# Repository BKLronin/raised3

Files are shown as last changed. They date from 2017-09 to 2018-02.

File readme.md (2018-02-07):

# raise-d³ #

## Description ##

FDM printer for remote operation with octoprint for flexible small scale production. Designed from scratch and inspired by the I3 by Josef Prusa, MP3DP by Ryan Zellar and the Itopie by Skarab

### Key features ###

Print volume: 250 x 270 x 250

Made from 12mm beechplywood "Multiplex"

Exchangeable extrudermount with E3D Titan Aero as suggested standard. Should fit a MK8 Style extruder and hotend as well. 

The electronic parts are all kept within the main case and get cooled by two 60mm fans.

Not designed yet but should work with a small spindle like Proxxon or Dremel for carving PCB production.

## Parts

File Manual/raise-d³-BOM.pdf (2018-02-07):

Raise-d³ | BOM
| Mechanik
Bauteil | Anzahl | Beschreibung | Preis in EUR | Quellenbeispiel
D³ – Multiplex Rahmenset | 1 | Buchenmultiplexrahmen cnc gefräst | 119 | Raise-Shop, selbst
Gedruckte Teile Set | 1 | PLA/PETG | 89,99 | Raise-Shop, selbst
Aluminumbett | 1 | 6mm feinstgefräst | 25 | B&T Metall
Präzisionswelle 400mm | 4 | Gehärtet h6¹ | 25 | Dold_Mechatroni k
Präzisionswelle 390mm | 2 | Gehärtet h6 | 15 | Dold
Wellenhalter H10 stehend | 8 | Kann gedruckt werden | 30 | Dold
LM10UU Lager | 12 | Gedruckte oder IGUS lager möglich | 5 | Dold
Kugellager 608 | 3 | Für Y Riemen umlenk, Spule | 1 | Dold
Kugellager ID4mm | 1 | Für X idler
GT2 Riemen X | 1 | 1m
GT2 Pulley | 1 | 21 Zähne | 2
HTD Riemen Y | 1 | 1m HTD3m 9mm, PU | | Dold
HTD Pulley | 1 | 20 Zähne HTD3m, 9mm, breit 5mm Bohrung | | Dold
Gewindespindel | 2 | TR 8x1,5, 300mm, Alternativ integrierte von anycubic | 5 | Dold
Kupplung | 2 | 5mm auf 8mm. Gedruckt TPU | 5 | raise-shop
M4 x 16 | 70
M4 x 20 | 11
M4 x16 senk | 16
M4 x25 | 2
M3 x20 | 4
M3 x30 | 1
M3 x16 | 22
M3 x40 /2x 16 | 1/2
M3 x10 | 12
M3 Mutter Selbstsichernd | 18
| | | 0

Elektronik
Bauteil | Anzahl | Beschreibung | Preis in EUR | Quellenbeispiel
Steppermotor | 4 | 4 x Nema 17 | 50 | stepper-online
Mainboard | 1 | Megatronics / Minitronics | 90/50 | reprapworld
Rapsberry Pi3 | 1 | + Sd Card | 40 | reichelt
Raspicam | 1 | Optional + längeres Flachband | 25 | teichelt
Netzteil | 1 | Meanwell 10A(LRS-100-12 ) für Silikon oder 30 A für das kleinere MK2ish Heizbett | | Rs components
Heizmatte | 1 | 250 x 250 mm 230V | 50 | filafarm
SSR | 1 | 12V DC in 230 V Schalt | 20 | reichelt
Hotend/Extruder | 1 | E3D Titan Aero | 130 | E3D-online
Hauptschalter | 1 | WS R13-112 LPLB | 1 | reichelt
Sicherung | 1 | TR 3,15 A | ,2 | reichelt
Kaltgerätestecker | 1 | KES 2SI | | reichelt
Lüfter Radial | 1 | EBM Papst RLF35 | 25 | rs-components
Lüfter Hotend | 1 | EBM Papst 412 (optional) | 15 | reichelt
Lüfter Gehäuse | 2 | Skythe MK60 | 9 | reichelt
5V 2A Regulator | 1 | Servo + Raspi (RECOM) | 5 | reichelt
Servo 9g | 1 | Hitec HS65 / KDS | 20
Sum | 390,2

1

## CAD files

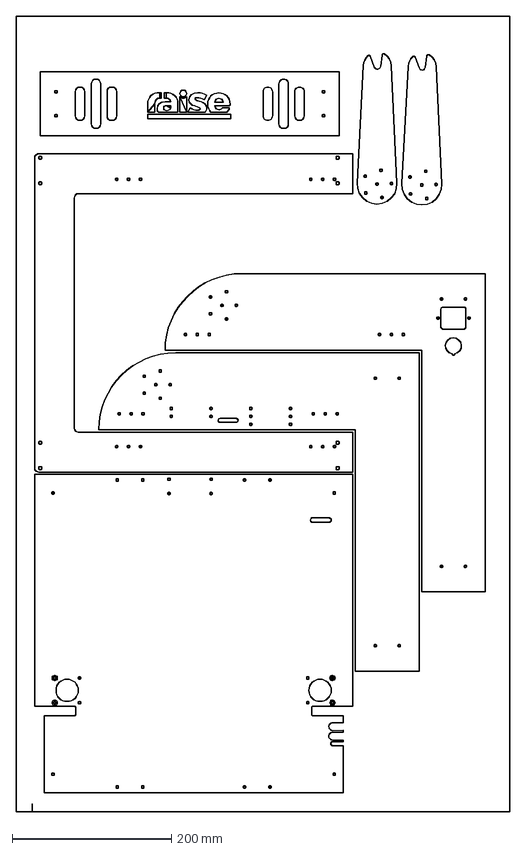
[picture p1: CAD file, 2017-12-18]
Milled_Parts/#raiseuav komplett 2017_09_16.dxf
620.0 x 1000.0 mm

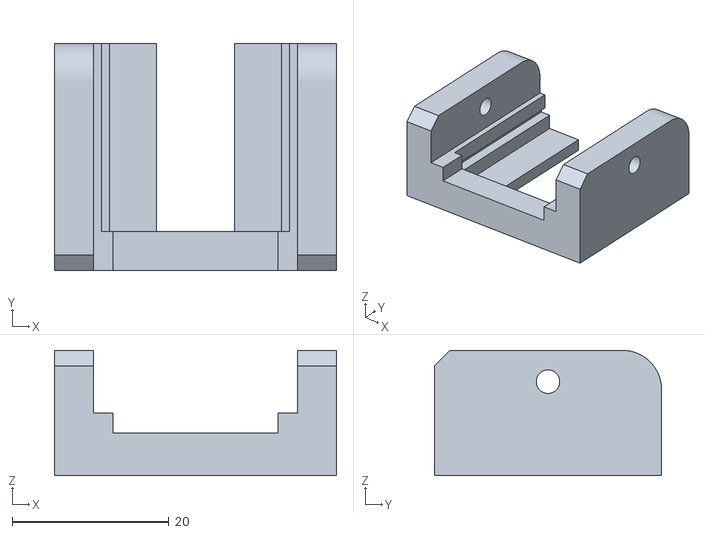
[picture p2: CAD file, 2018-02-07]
Printed_Parts/raspicam_arm_pcb.stl
36.0 x 29.0 x 16.0

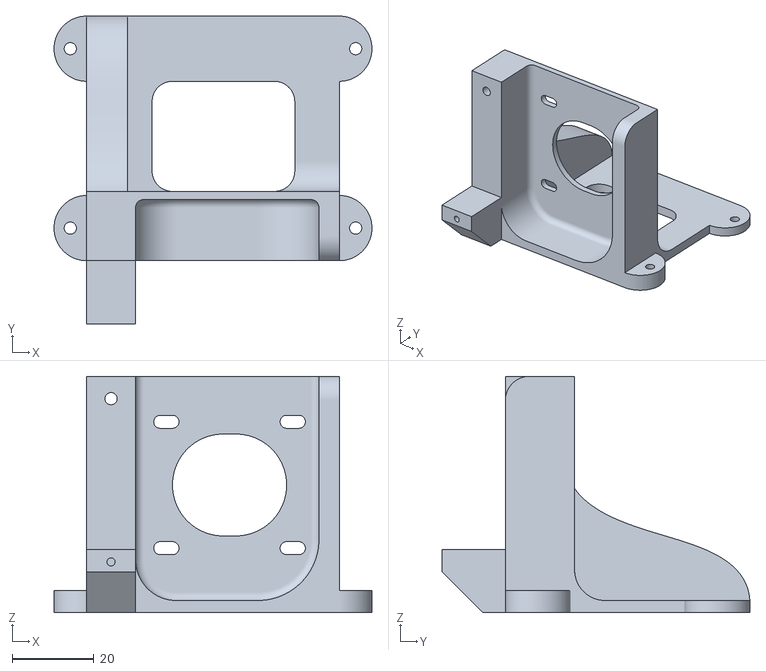
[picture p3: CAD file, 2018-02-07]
Printed_Parts/Aero_Frame.stl
78.0 x 75.5 x 58.0

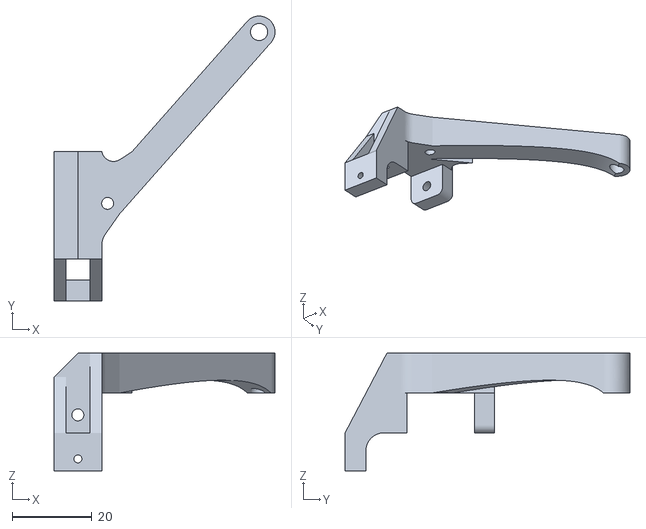
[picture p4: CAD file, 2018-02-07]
Printed_Parts/Axialfan_Mount.stl
55.5 x 71.5 x 29.5

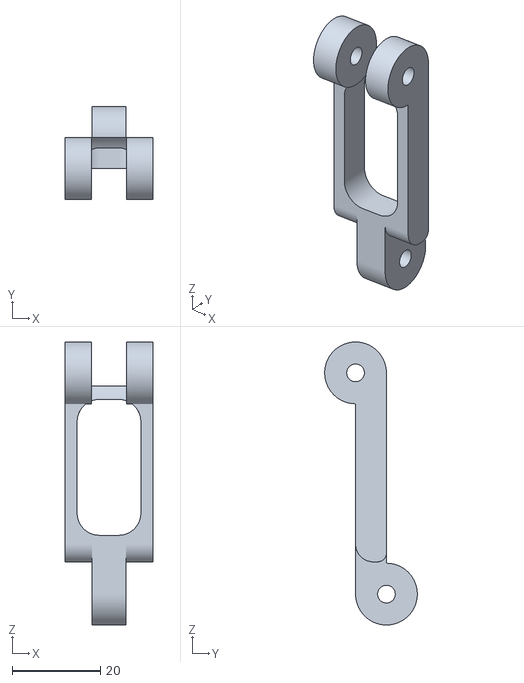
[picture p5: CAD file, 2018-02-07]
Printed_Parts/raspicam_arm_lower.stl
20.0 x 20.9 x 64.0

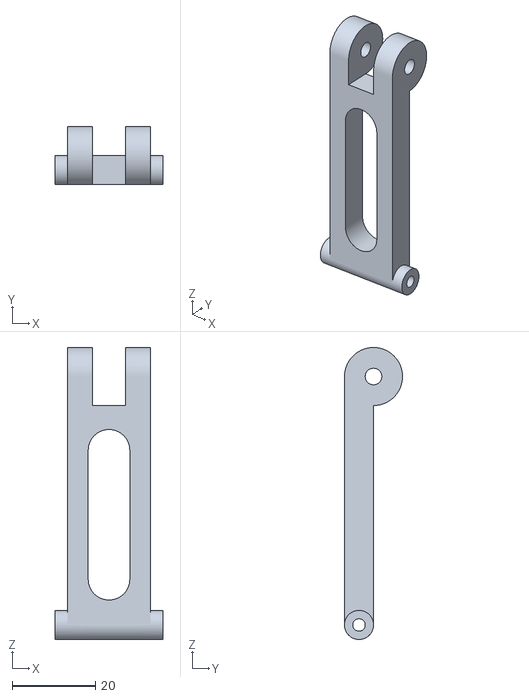
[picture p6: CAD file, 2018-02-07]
Printed_Parts/raspicam_arm_upper.stl
26.0 x 14.0 x 70.2

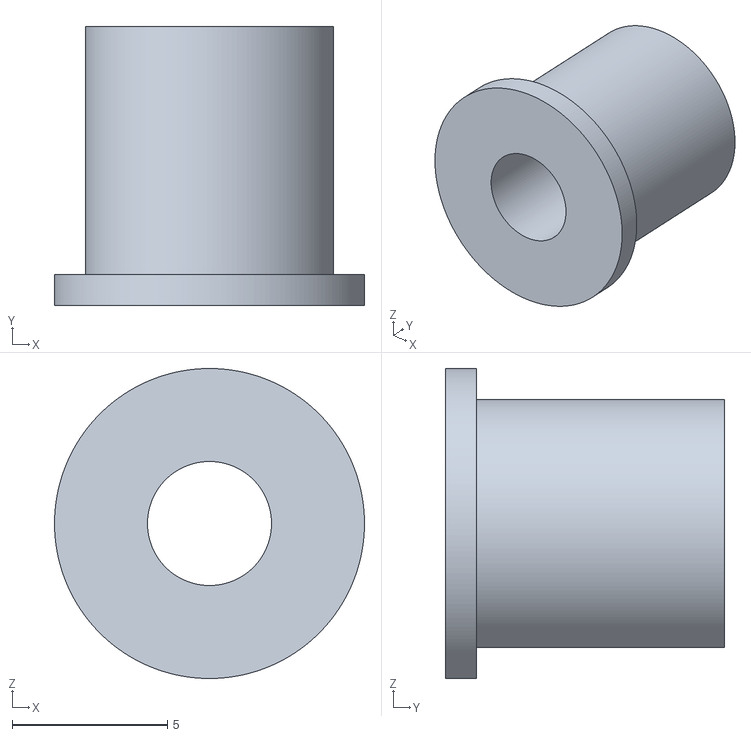
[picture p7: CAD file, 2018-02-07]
Printed_Parts/Y-608Adapter8-4.stl
10.0 x 9.00 x 10.0

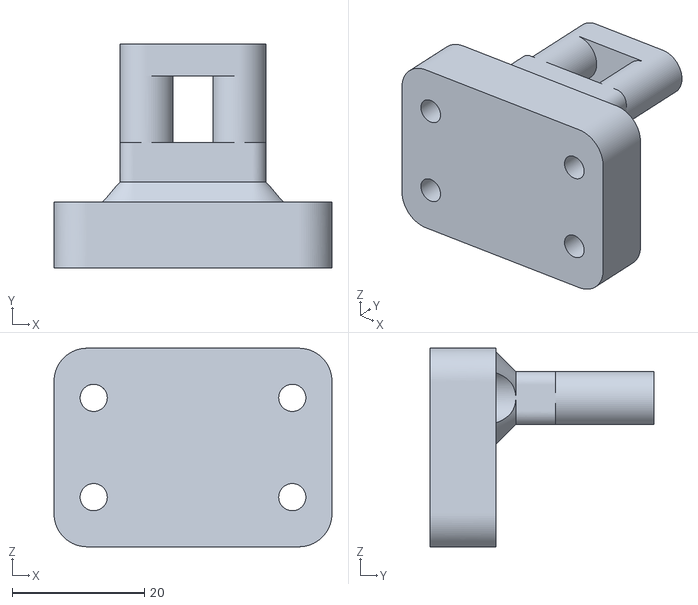
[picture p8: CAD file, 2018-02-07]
Printed_Parts/Y-Bed-Belt_Anchor_NewB.stl
42.0 x 33.9 x 30.0

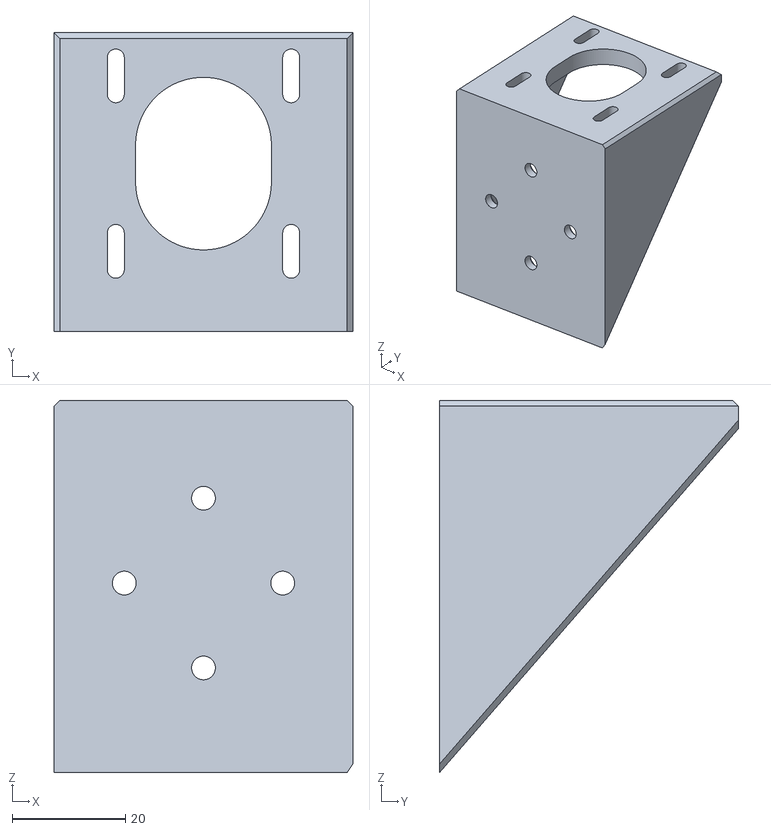
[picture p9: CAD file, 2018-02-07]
Printed_Parts/Nema17-Y-Stepper_Holder_AdjustB.stl
52.8 x 52.8 x 65.8

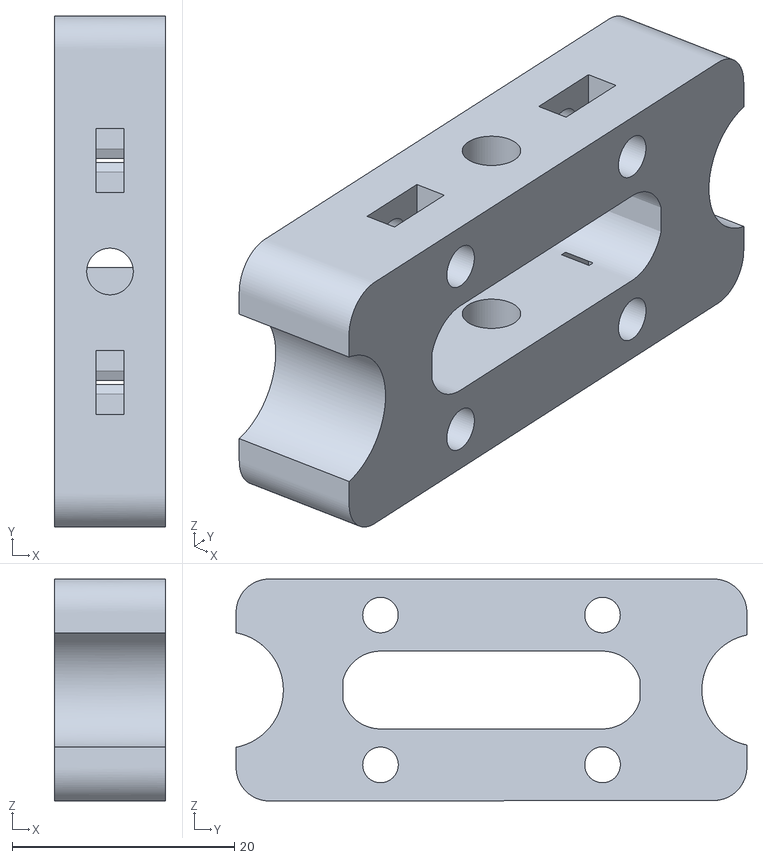
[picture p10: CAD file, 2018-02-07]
Printed_Parts/X-Bearing_Holder_AdjustB(Alternat).stl
10.0 x 46.0 x 20.0

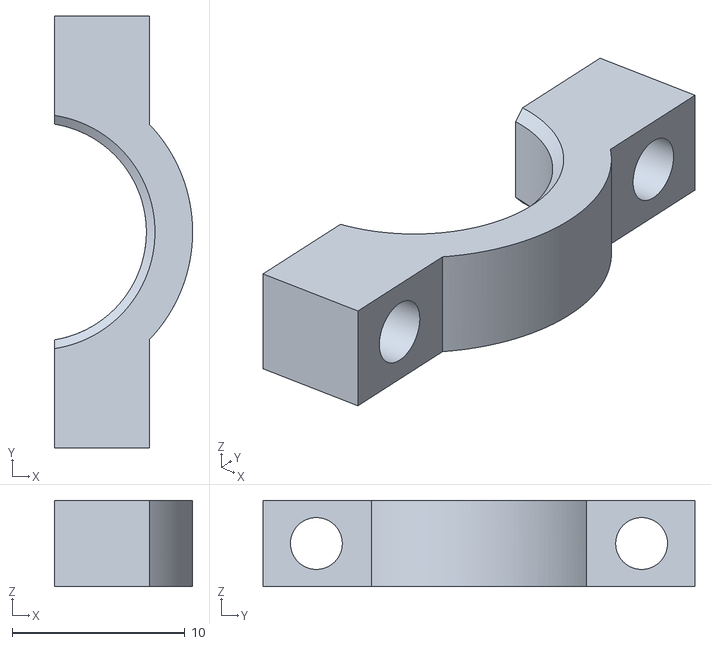
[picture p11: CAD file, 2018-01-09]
Printed_Parts/X-carriage_cable.stl
8.00 x 25.0 x 5.00

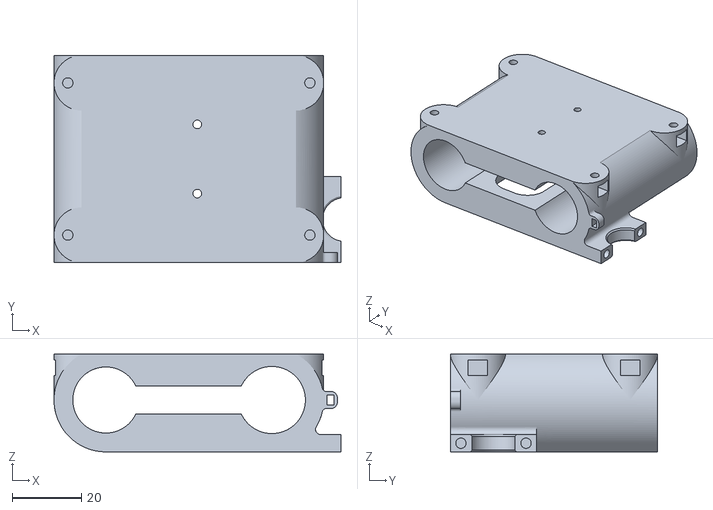
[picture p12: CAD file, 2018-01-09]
Printed_Parts/X-carriage.stl
83.0 x 60.0 x 28.3

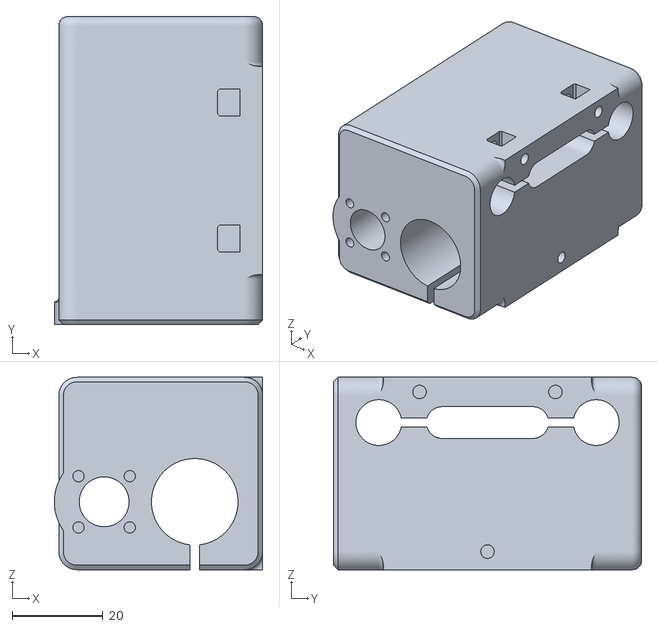
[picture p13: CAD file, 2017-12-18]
Printed_Parts/XZ-Block_right.stl
46.0 x 68.0 x 42.5

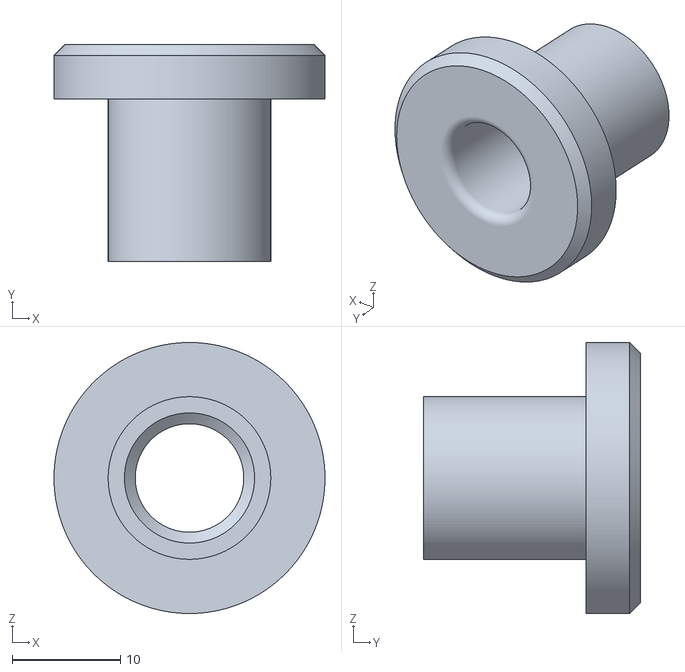
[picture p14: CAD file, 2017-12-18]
Printed_Parts/Cableduct_bed.stl
25.0 x 20.0 x 25.0

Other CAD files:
Printed_Parts/Nema17-Y-Stepper_Holder.stl
Printed_Parts/XZ-Block_left.stl
Printed_Parts/raspicam_arm_foot.stl
Printed_Parts/Y-Beltbed_adjustment_Stat.stl
Printed_Parts/Angle_Portal.stl
Printed_Parts/BedEdgeclamp.stl
Printed_Parts/Cooling_Exhaust.stl
Printed_Parts/Fanduct.stl
Printed_Parts/FrameAngle_lower.stl
Printed_Parts/Nema14_Stepper_Holder.stl
Printed_Parts/SpoolDrum.stl
Printed_Parts/SpooldrumNut.stl
Printed_Parts/TPU_coupling30pctI.stl
Printed_Parts/X-Bearing_Holder.stl
Printed_Parts/X-BeltClamp.stl
Printed_Parts/Y-Bearing_Holder.stl
Printed_Parts/Y-Bed_Bearing_holder.stl
Printed_Parts/Y-Beltbed_adjustment_Move.stl

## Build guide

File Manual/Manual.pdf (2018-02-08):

raise-d³ | Handbuch

## Inhaltsverzeichnis

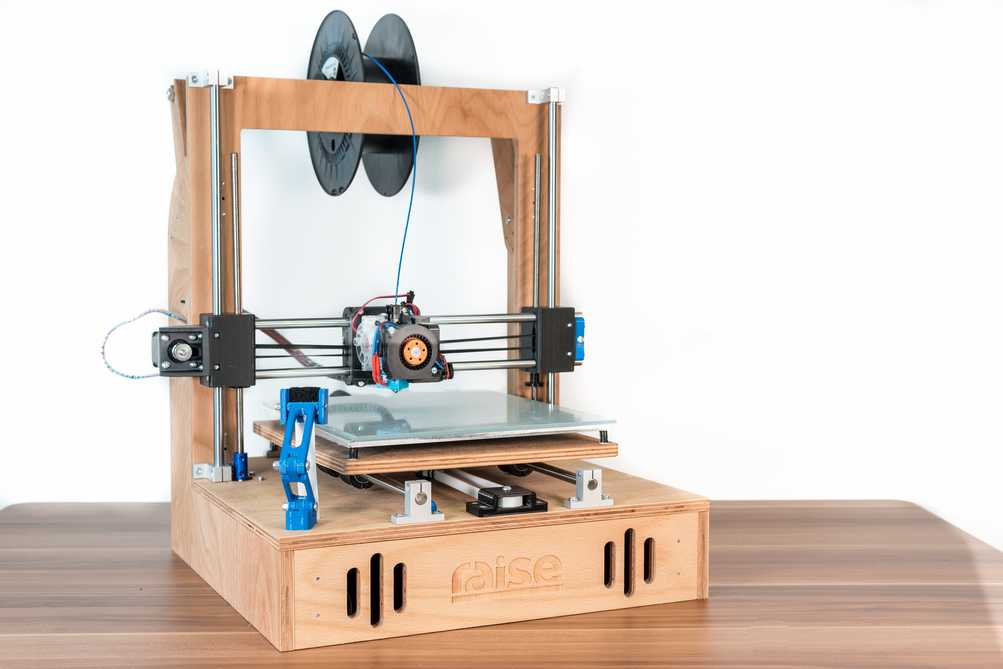
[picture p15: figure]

## 1. Introduction

## 1.1. Safety instructions

The printer has a number of safety circuits, but never leave it unattended.

Do not lift the printer while the power plug is plugged in. There is a risk of electric shock.

Keep the pressure chamber clear. Handling within the installation space can cause injuries.

Never touch the heating components while the printer is switched on, as this may cause burns.

Use suitable fire extinguishers in case of fire to avoid the danger of an electric shock.

Have maintenance work on the electronics and mechanics carried out by a service technician to prevent damage.

The current-carrying components should be connected by a trained electrician (VDE)! The company raise-UAV assumes no liability for damages and injuries resulting from faulty installations.

## 2. Build the Printer

## 2.1. Manufacturing of the frame

Beech plywood with a thickness of <= 12mm was used for the frame. The panels have a maximum dimension of 400mm in all directions. A little reserve when milling is to be considered. Milling was done with a 3mm universal 2-flute or 3mm diamond cut.

Milling parameters for beech plywood (MPCNC):
400 mm/min at 3mm immersion depth conventional (clockwise)
800W spindle at 30000 revolutions

Panel blanks with 450 x 450mm were used, which enables individual turning of the panels so that during assembly the curvature lies outside and can be pulled against the milling edge.
When drilling the holes (CNC), a helical movement of at least 0.5mm (at 3mm milling cutter) must be observed to ensure chip removal.

The holes should not exceed 3.5mm as these threads are drilled with a 4mm tap.
All 3mm holes in the drawing are therefore provided with an M4 thread which is necessary for the connection with the printed angles.

### 2.2 Post processing the plates

Grinding was done with a triangular grinder (depending on availability) to get the surface as smooth as possible for impregnation.
Polyboy wood oil has proved its worth since it cannot ignite itself and offers sufficient protection of the wood without toxic components. It can also be used indoors without the risk of solvents in the room air. Alternatively, the panels can of course also be painted. The oil is ideally applied after the frame has been mounted to relieve a bit of the tension.

## 2.3 Printing the parts

All parts can be printed in PLA with a minimum infill of 30%. The Nema14/17X holder should be made of temperature-resistant materials. In this case Greentec was used which withstands temperatures up to 60°C without any problems. With the larger Nema17 mount, the temperature is expected to be lower, so PLA or better PETG is completely adequate at this point. The extrudermount for the Titan Aero or MK8 extruder can also be printed from more thermostable materials.

## 2.4. Frame assembly

The frame is held together by two types of angles. They compensate and dampen possible distortion in the plywood panels and are easy to produce.

The angles are fixed with M4 x 16 mm screws in the previously cut threads in the plywood panels M4. Explosionsanimation (https://www.youtube.com/edit?o=U&video_id=dvnm-ai_ZwE)

Start with the two side panels, the base plate, the front and back plates. It is recommended that the installation is carried out on a level ground. When tightening the screws make sure that nothing is distorted. The frame is largely self-aligning. Finally, the portal with any existing curvature is inserted in the direction of the logo and pulled backwards with the portal angles against the side panels.

•

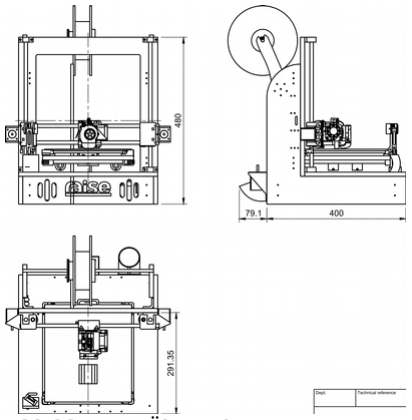
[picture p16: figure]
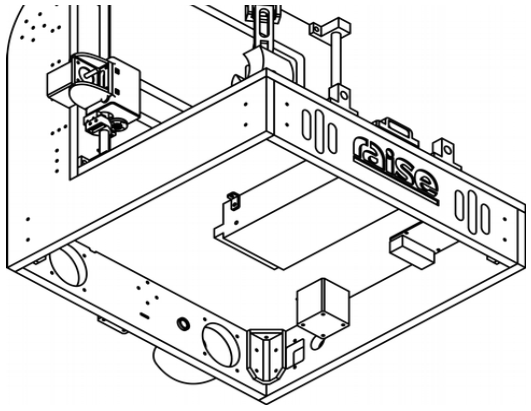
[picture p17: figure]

Abbildung 1: Übersicht | Abbildung 2: Position Winkel

## 2.5 Component placement

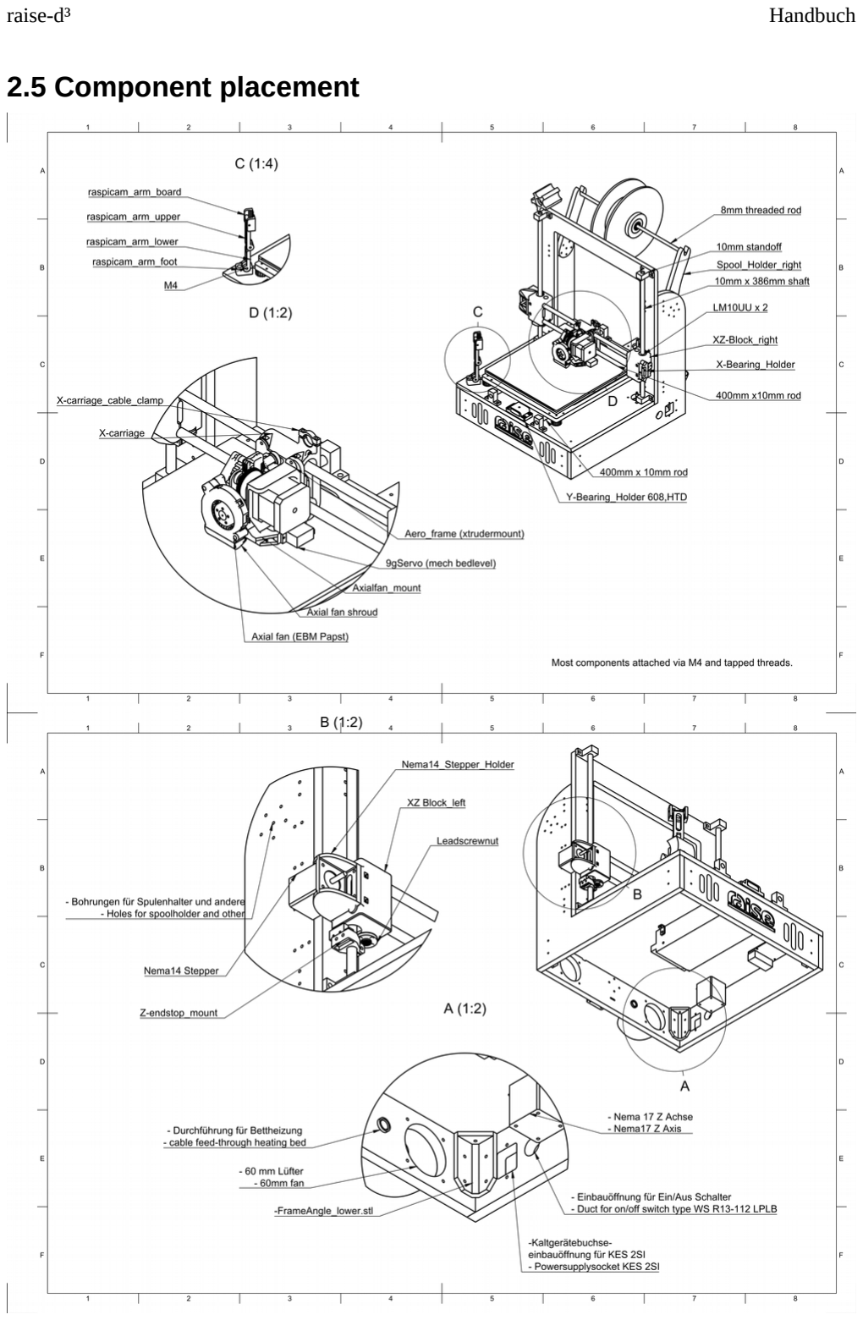
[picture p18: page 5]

## 2.6. Axis installation

### 2.6.1 Y-Axis

Push the LM10UU bearings into the "Y-Bed_Bearing_holder" and loosely screw them with M4x16 onto the underside of the bed. The bearings are fixed with M3 x 20 in the holders. Take one of the 10 x400mm precision shafts and slide it into the bearings to align them. While the shaft is in it, tighten the brackets crosswise. The shaft should move easily. Repeat this procedure for the second page.

Screw the belt holder "Y-Beltbed_adjustment_Stat" with four M4 x 16 screws to the underside of the bed. Insert an M3 locknut into the hexagon nut on the fixed side (Fig.
4) and an M3x30 into the movable side (Fig. 5). The movable side is now inserted into the T_slot of the fixed side and tightened slightly with the M3 screw. These two parts later ensure that the Y-belt is tensioned.

Fasten the "Nema17-Y-Stepper_Holder" (Fig. 6) to the rear of the frame with four M4x16 screws and a Nema 17 with approx. 40N/cm with M3 x16 loose in it. Attach the HTD Pulley to the axis of the stepper.
Screw the "Y-Bearing_Holder" (Fig. 7) with countersunk head M4 x 16 onto the base plate and fix a 608 ball bearing with washers in it. There is an adapter for the M8 to M4 in the printed parts directory.

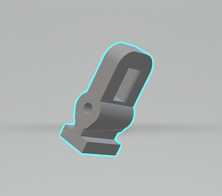
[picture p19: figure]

Guide the strap through all components around the pulley and secure it as tightly as possible on both sides of the tensioning mechanism with cable ties. It is recommended to fix one side of the Y-mechanism on the base plate with M4 x16 and to tilt the bed slightly when tightening. Continue tightening the belt by tightening the stepper motor and after securing the second linear guide, adjust the tension to the desired tension using the M3 screw on the belt attachment.

The aluminium bed is made of a finely milled cast aluminium piece of 250x280x6mm. The holes correspond to those in the bed and are screwed with M4 countersunk head screws and springs into the M4 threads of the bed.

An insight into the alignment of an older version of the printer is given below hier (https://youtu.be/frliOqVh3j4?t=1m12s)

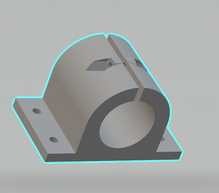
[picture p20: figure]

Abbildung 3

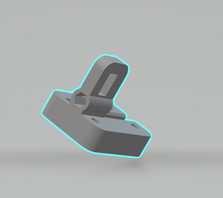
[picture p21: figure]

Abbildung 4

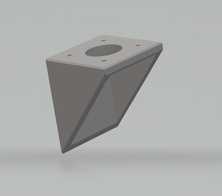
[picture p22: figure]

Abbildung 6

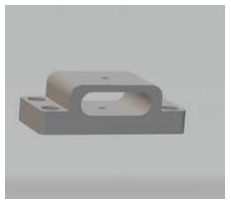
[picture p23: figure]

Abbildung 7

Abbildung 5

### 2.6.2 X-Axis

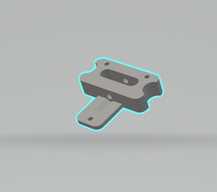
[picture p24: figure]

Drill the holes in part "XZ-Block_left" and "XZ-Block_right" as shown in Figure 9, attach the "Nema14_Stepper_Holder" to the left X-Z block with M3 x 16 and corresponding lock nuts.
Insert the 10 x 400 mm precision shaft into the 10 mm openings up to the stop of the stepper holder in the left X-Z_Block, where more force may be required.
Drill all holes to 3mm. Take four LM10UUU bearings and slide them into the "Xcarriage" (Fig. 11). Then push it onto the rods. If the bearings are too loose, they can be locked with a layer of tesa.
Slide the "XZ-Block_right" onto the two shafts and attach the "X-Bearing_Holder" to the "XZ-Block_right". The shafts should be flush with the surface of the bearing support + 2mm, for example, the exact alignment is done when merging with the Z-axis.
Drill the "X-BeltClamp" (Fig. 12) to 3mm and fasten it in the pocket of the "Xcarriage" with long enough M3 and nuts on the opposite side.
Connect the stepper motor and the moving part to the GT2 belt through the bearing on the opposite side. Leave the stepper loose so that you can retighten it later.

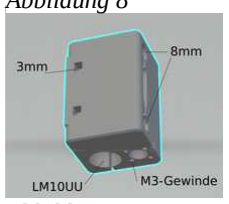
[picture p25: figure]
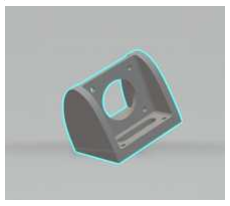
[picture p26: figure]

Abbildung 10

Abbildung 8

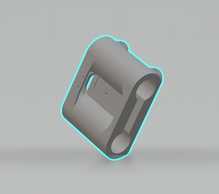
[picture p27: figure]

Abbildung 11

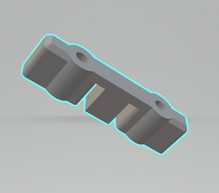
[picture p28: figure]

Abbildung 12

Abbildung 9

### 2.6.3 Z-Axis

Install the Nema17 Stepper with M3 screws in the base plate. Now screw the lower shaft holders into the holes of the portal. Then they take the 390mm precision shafts and insert them into the holders as far as they will go. Screw the guide spindles into the spindle axis nuts of the X-axis and guide the entire assembly on both sides onto the Z-axis shafts. Couple the leadscrews with the stepper motors in the base plate to the printed TPU coupler (or other). Alternatively: Integrated leadscrews. Now install the upper shaft holders.
Check the distance of the X-Z-blocks to each other and make sure that they do not cause any tension between the Z-shafts. Correct these if necessary.

Translated with www.DeepL.com/Translator

1. Einfuehrung
1.1. Sicherheitshinweise
1.2. Lieferumfang
1.3. Technische Details
2. Montage des Druckers
2.1. Aufbau des Rahmens
2.2. Installation der Linearmechanik
2.3. Installation der elektronischen Komponenten
2.4. Verkabelung
2.5. Ausrichten des Druckbetts
3. Software
3.1. Cura installation
3.2. WLAN Einrichtung
3.3. Koppeln des Druckers mit Cura
4. Allgemeiner Workflow
5. Support
6. Rechtliches

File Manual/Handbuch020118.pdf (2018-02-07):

raise-d³ | Handbuch

## Inhaltsverzeichnis


## 1. Einfuehrung

## 1.1. Sicherheitshinweise

Der Drucker verfügt über eine Reihe von Sicherheitsschaltungen, lassen sie ihn dennoch niemals unbeaufsichtigt.

Heben sie den Drucker nicht an solange der Netzstecker am Gerät eingesteckt ist. Es besteht die Gefahr eines elektrischen Schocks.

Halten sie den Druckraum frei. Das hantieren innerhalb des Bauraums kann zu Verletzungen führen.

Berühren sie niemals die Heizkomponenten während der Drucker eingeschaltet ist, dies kann zu Verbrennungen führen.

Verwenden sie im Brandfall geeignete Feuerlöscher um der Gefahr eines elektrischen Schocks zu entgehen.

Lassen sie Wartungsarbeiten an der Elektronik und Mechanik von einem Servicetechniker durchführen um Schäden zu vermeiden.

Der Anschluss der Stromführenden Komponenten sollte von einem hierfür ausgebildeten Elektriker(VDE) erfolgen! Die Firma raise-UAV übernimmt keine Haftung für Schäden und Verletzungen die aus fehlerhaften Installationen entstanden sind.

## 2. Montage des Druckers

## 2.1. Herstellen des Rahmens

Für den Rahmen wurde Buchensperrholz mit einer Stärke von <= 12mm verwendet. Die Platten haben ein Maximalmaß von 400mm in alle Richtungen. Ein wenig Reserve beim Fräsen ist einzuplanen. Gefräst wurde mit einem 3mm Universalzweischneider oder 3mm Diamantschliff. Fräsparameter für Buchensperrholz:
- 300 mm/min bei 3mm Eintauchtiefe konventionell (Uhrzeigersinn)
- 800W Spindel bei 30000 Umdrehungen
Verwendet wurden Plattenzuschnitte mit 450 x 450mm dies ermöglicht ein individuelles drehen der Platten so dass bei der Montage die Krümmung außen liegt und gegen die Fräskante gezogen werden kann.
Beim Bohren der Löcher (CNC) ist eine Kreisbewegung mit mindestens 0,5mm (bei 3mm Fräser) zu achten um die Spanabfuhr zu gewährleisten.
Die Bohrungen sollten 3,5mm nicht übersteigen da in diese Gewinde mit einem 4mm Gewindebohrer gesetzt werden.
Alle in der Zeichnung befindlichen 3mm Bohrungen werden somit mit einem M4 Gewinde versehen das für die Verbindung mit den gedruckten Winkeln notwendig ist.

## 2.2 Nachbearbeitung der Platten

Geschliffen wurde mit einem Dreiecksschleifer (je nach Verfügbarkeit) um die Oberfläche so glatt wie möglich für die Imprägnierung zu bekommen.
Bewährt hat sich Polyboy Holzöl da dieses sich nicht selbst entzünden kann und einen ausreichenden Schutz des Holzes ohne giftige Bestandteile bietet. Es lässt sich zudem gut in Innenräumen anwenden ohne die Gefahr von Lösungsmittel in der Raumluft. Alternativ können die Platten natürlich auch lackiert werden.

## 2.3 Herstellen der Druckteile

Alle Teile können in PLA mit einer Mindestfüllung von 30 % gedruckt werden. Der Nema14X_halter sollte mit temperaturfesteren Materialien ausgeführt werden. In diesem Fall wurde Greentec verwendet das den Temperaturen bis 60°C ohne weiteres widerstand. Bei der größeren Nema17 Halterung ist mit weniger Temperatur zu rechnen daher ist PLA oder besser PETG an dieser Stelle völlig ausreichend. Der Hotendhalter für den Titan Aero oder MK8 Extruder kann ebenfalls aus Thermostabileren Materialien gedruckt werden.

## 2.4. Zusammensetzen des Rahmens

Der Rahmen wird durch die zwei Arten von Winkeln zusammengehalten. Dabei kompensieren und dämpfen sie eventuellen Verzug in den Sperrholzplatten und sind leicht herzustellen.

Die Winkel werden mit M4 x 16 mm Schrauben in den vorher geschnittenen Gewinden in den Sperrholzplatten M4 befestigt. Explosionsanimation (https://www.youtube.com/edit?o=U&video_id=dvnm-ai_ZwE)

Begonnen wird mit den beiden Seitenteilen, der Bodenplatte, den Front und Rückplatten. Es empfiehlt sich die Montage auf möglichst ebenem Grund auszuführen. Beim festziehen der Schrauben darauf achten das nichts verzogen wird. Der Rahmen richtet sich größtenteils selbst aus. Als letztes wird das Portal mit der evtl vorhandenen Wölbung Richtung Logo eingesetzt und nach hinten mit den Portalwinkeln gegen die Seitenteile gezogen.

•


Abbildung 1: Übersicht | Abbildung 2: Position Winkel

## 2.5 Lage der Komponenten

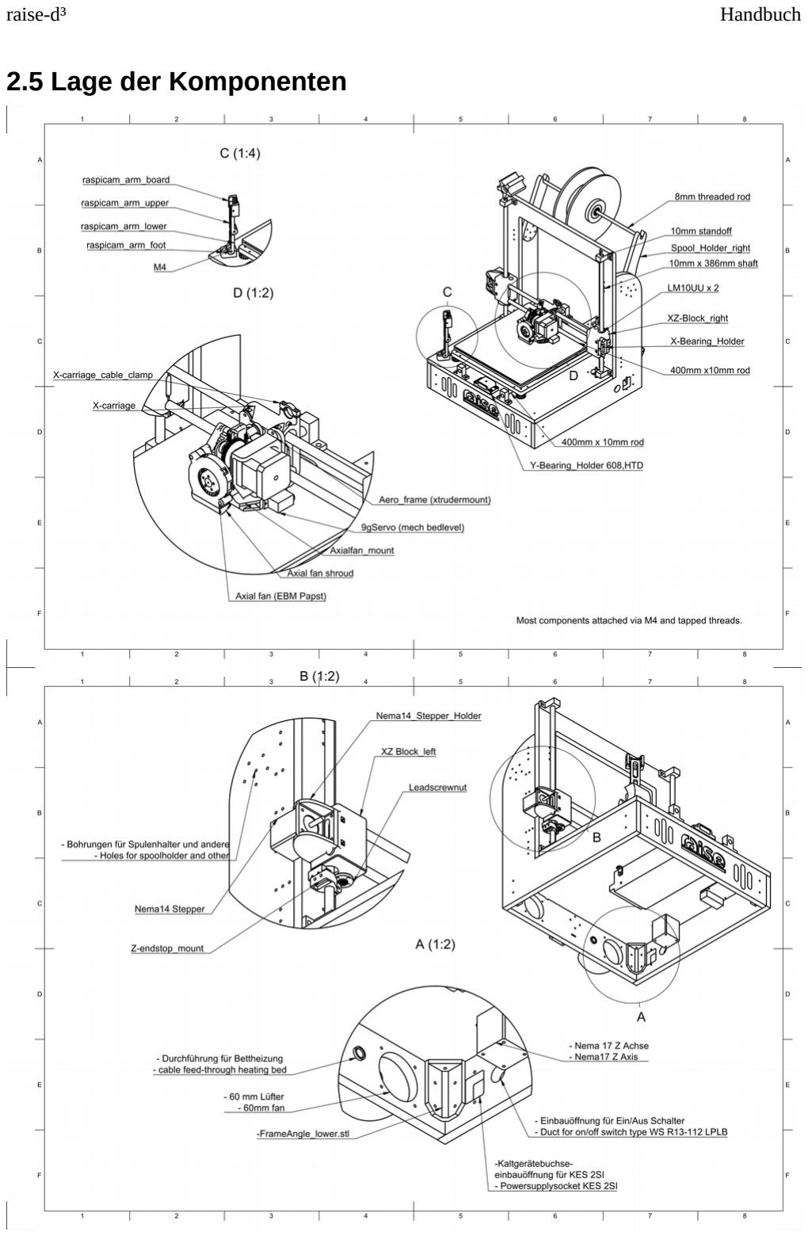
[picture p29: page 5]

## 2.6. Installation der Achsen

### 2.6.1 Y-Achse

Schieben sie die LM10UU Lager in die „Y-Bed_Bearing_holder“ und Schrauben sie diese lose mit M4x16 auf die Unterseite des Betts. Die Lager werden mit M3 x20 in den Haltern fixiert. Nehmen sie eine der 10 x400mm Präzisionswellen und schieben sie sie in die Lager um diese ausrichten. Während sich die Welle darin befindet schrauben sie die Halter über Kreuz fest. Die Welle sollte sich leicht bewegen lassen. Wiederholen sie diesen Vorgang auch für die zweite Seite.

Schrauben sie den Riemenhalter „Y-Beltbed_adjustment_Stat“ mit vier M4 x16 Schrauben an die Unterseite des Betts. Führen sie eine M3 Sicherungsmutter in die Sechskantmutter der festen Seite (Abb4) und eine M3x30 in die bewegliche Seite (Abb5). Die bewegliche Seite wird nun in die T_Nut der festen Seite eingeschoben und mit der M3 Schraube leicht vorgezogen. Diese beiden Teile sorgen später für das spannen des Y-Riemens.

Befestigen sie den „Nema17-Y-Stepper_Holder“ (Abb6) an der Rückseite des Rahmens mit vier M4x16 Schrauben und einen Nema 17 mit ca 40N/cm mit M3 x16 lose in diesem. Befestigen sie den HTD Pulley auf der Achse des Steppers. Schrauben sie den „Y-Bearing_Holder“ (Abb7) mit Senkkopf M4 x 16 auf die Bodenplatte und fixieren sie ein 608er Kugellager mit Unterlegscheiben in diesem.


Führen sie den Riemen durch alle Komponenten um den Pulley herum und fixieren sie ihn auf beiden Seiten der Spannmechanik mit Kabelbindern so straff wie möglich. Es empfiehlt sich bereits eine Seite der Y Mechanik auf der Bodenplatte mit M4 x16 zu fixieren und das Bett leicht anzukippen beim festziehen. Spannen sie den Riemen weiter mit dem festziehen des Steppermotors und stellen sie nach dem befestigen der zweiten Linearführung die Spannung mit der M3 Schraube an der Riemenbefestigung auf die gewünschte Spannung ein.

Das Aluminiumbett wird aus einem feinstgefrästen Gußaluminumstück mit 250x280x6mm gefertigt. Die Bohrungen entsprechen denen im Bett und werden mit M4 Senkkopfschrauben und Federn in die M4 Gewinde des Betts geschraubt.

Ein (https://youtu.be/frliOqVh3j4?t=1m12s) Einblick in die Ausrichtung einer älteren Version des Druckers gibt es gibt es hier (https://youtu.be/frliOqVh3j4?t=1m12s)


Abbildung 3


Abbildung 4


Abbildung 6

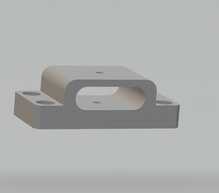
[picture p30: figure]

Abbildung 7

Abbildung 5

### 2.6.2 X-Achse


Bohren sie die Löcher im Teil „XZ-Block_left“ und „XZ-Block_right“ wie in Abbildung 9. Befestigen sie den „Nema14_Stepper_Holder“ am linken X-Z Block mit M3 x 16 und entsprechenden Sicherungsmuttern.
Führen sie die 10 x 400 mm Präzisionswelle in die 10mm Öffnungen bis zum Anschlag des Stepperhalters in den linken X-Z_Block hier kann ggf etwa mehr Kraft notwendig sein.
Bohren sie alle Löcher auf 3mm auf. Nehmen sie vier LM10UU Lager und schieben sie sie in das „X-carriage“ (Abb11). Schieben sie es anschließend auf die Wellen. Sollten die Lager zu locker sitzen können sie mit einer Lage Tesa etwas arretiert werden.
Schieben sie den „XZ-Block_right“ auf die beiden Wellen und befestigen sie den „X-Bearing_Holder“ am „XZ-Block_right“. Die wellen sollten etwa bündig mit der Oberfläche des Lagerhalters sein, die genaue Ausrichtung erfolgt bei der Zusammenführung mit der Z-Achse.
Bohren sie den „X-BeltClamp“ (Abb12) auf 3mm auf und befestigen sie ihn in der Tasche der „X-carriage“ mit genügend langen M3 und Muttern auf der Gegenseite. Verbinden sie mit dem GT2-Riemen den Steppermotor und den beweglichen Teil durch das Lager auf der Gegenseite. Lassen sie dabei den Stepper lose um später noch nachspannen zu können.

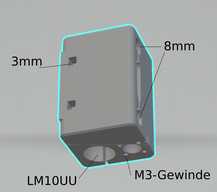
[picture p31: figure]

Abbildung 9

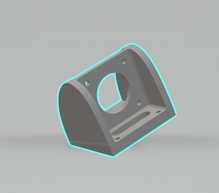
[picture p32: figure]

Abbildung 10

Abbildung 8


Abbildung 11


Abbildung 12

### 2.6.3 Z-Achse

Installieren sie die Nema17 Stepper mit M3 Schrauben in der Bodenplatte. Schrauben sie nun die unteren Wellenhalter in die Bohrungen des Portals. Anschließend nehmen sie die 390mm Präzisionswellen und stecken sie in die Halter bis zum Anschlag. Schrauben sie die Leitspindeln in die Spindelachsenmuttern der X-Achse und führen sie den gesamten Aufbau beidseitig auf die Z-Achsenwellen. Koppeln sie die Leitspindeln mit den Steppermotoren in der Bodenplatte mit dem gedruckten TPU Coupler (oder andere). Alternativ: Integrierte Leitspindeln. Installieren sie nun die oberen Wellenhalter.
Prüfen sie den Abstand der X-Z-Blöcke zueinander und stellen sie sicher das sie keine Spannung zwischen den Z Wellen verursachen. Korrigieren sie diese ggf.

1. Einfuehrung
1.1. Sicherheitshinweise
1.2. Lieferumfang
1.3. Technische Details
2. Montage des Druckers
2.1. Aufbau des Rahmens
2.2. Installation der Linearmechanik
2.3. Installation der elektronischen Komponenten
2.4. Verkabelung
2.5. Ausrichten des Druckbetts
3. Software
3.1. Cura installation
3.2. WLAN Einrichtung
3.3. Koppeln des Druckers mit Cura
4. Allgemeiner Workflow
5. Support
6. Rechtliches

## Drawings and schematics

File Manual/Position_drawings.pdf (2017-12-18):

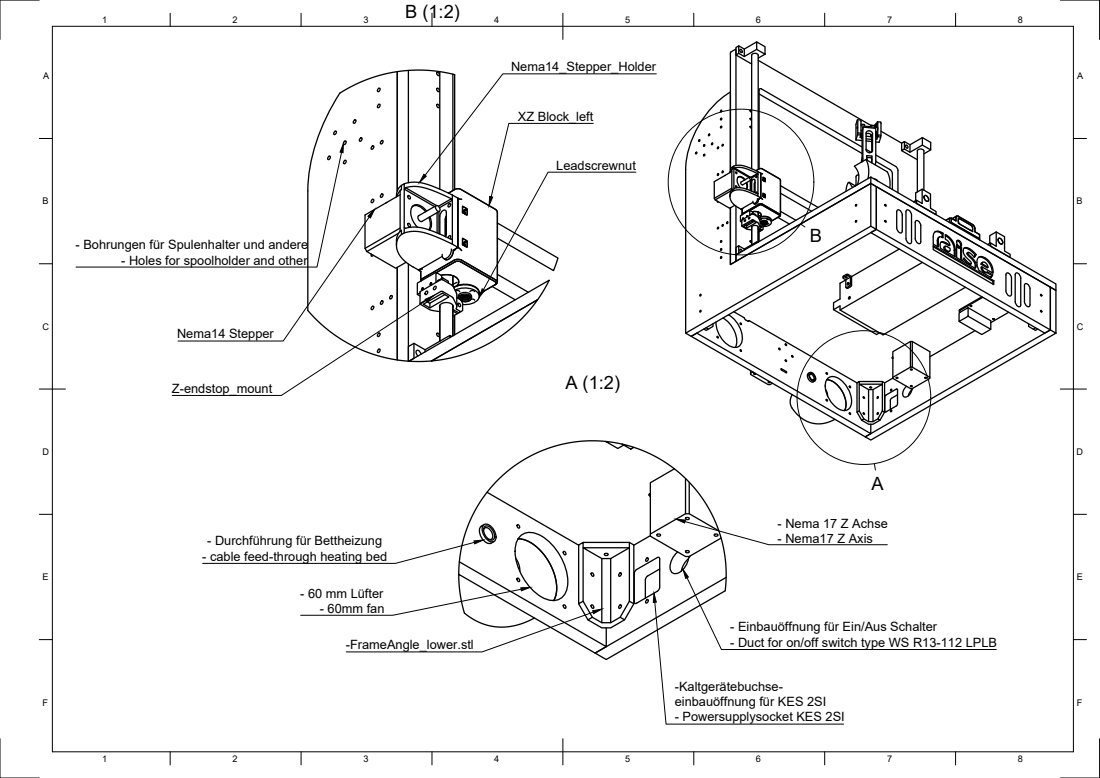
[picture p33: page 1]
- 60 mm Lüfter - 60mm fan; - Nema 17 Z Achse - Nema17 Z Axis; XZ Block_left; Nema14 Stepper

- Bohrungen für Spulenhalter und andere

- Holes for spoolholder and other

- Durchführung für Bettheizung
- cable feed-through heating bed

- Einbauöffnung für Ein/Aus Schalter
- Duct for on/off switch type WS R13-112 LPLB

-Kaltgerätebuchse-
einbauöffnung für KES 2SI
- Powersupplysocket KES 2SI

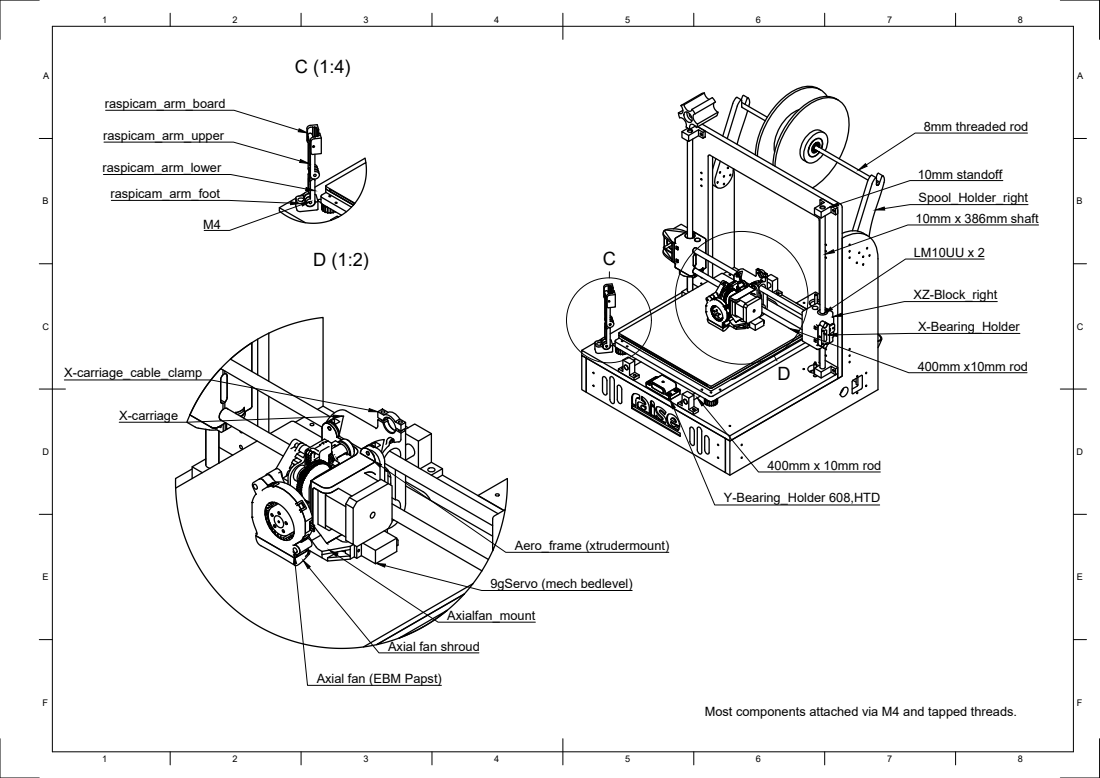
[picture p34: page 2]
10mm x 386mm shaft; 10mm standoff; 8mm threaded rod; 400mm x10mm rod; Y-Bearing_Holder 608,HTD; 400mm x 10mm rod; 9gServo (mech bedlevel); Aero_frame (xtrudermount)

Axial fan shroud

Axial fan (EBM Papst)

Most components attached via M4 and tapped threads.

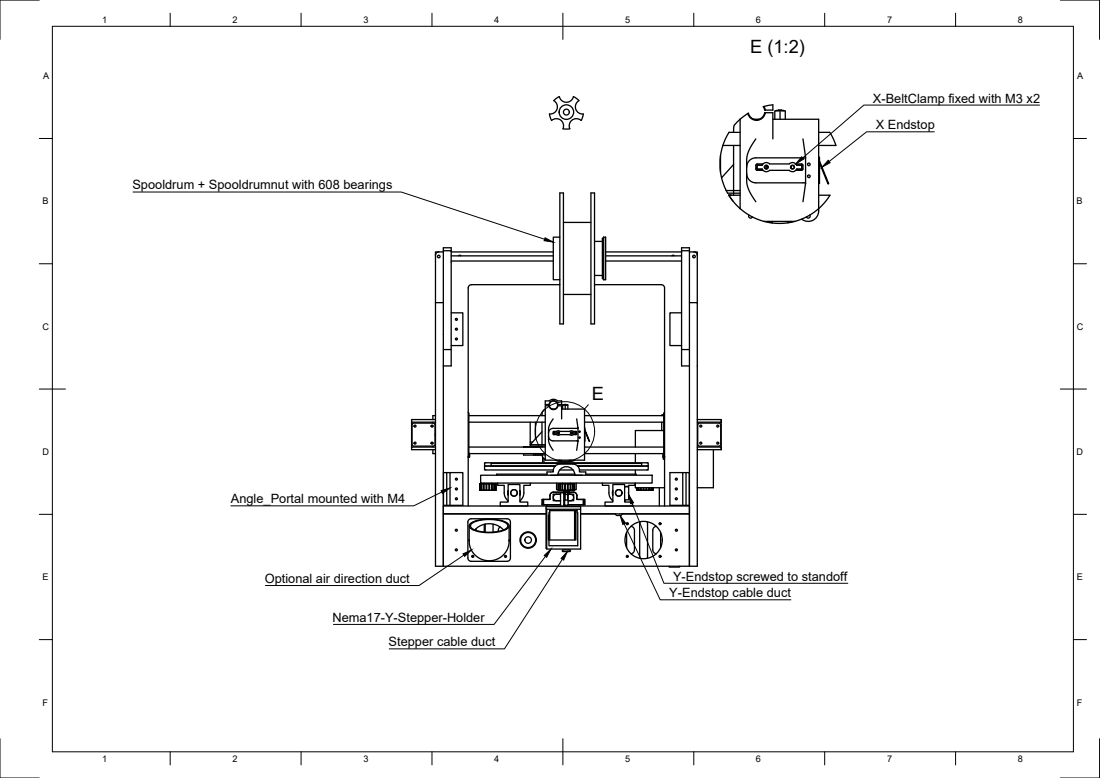
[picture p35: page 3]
X Endstop; Angle_Portal mounted with M4

X-BeltClamp fixed with M3 x2

Spooldrum + Spooldrumnut with 608 bearings

Y-Endstop screwed to standoff
Y-Endstop cable duct

Optional air direction duct

Stepper cable duct

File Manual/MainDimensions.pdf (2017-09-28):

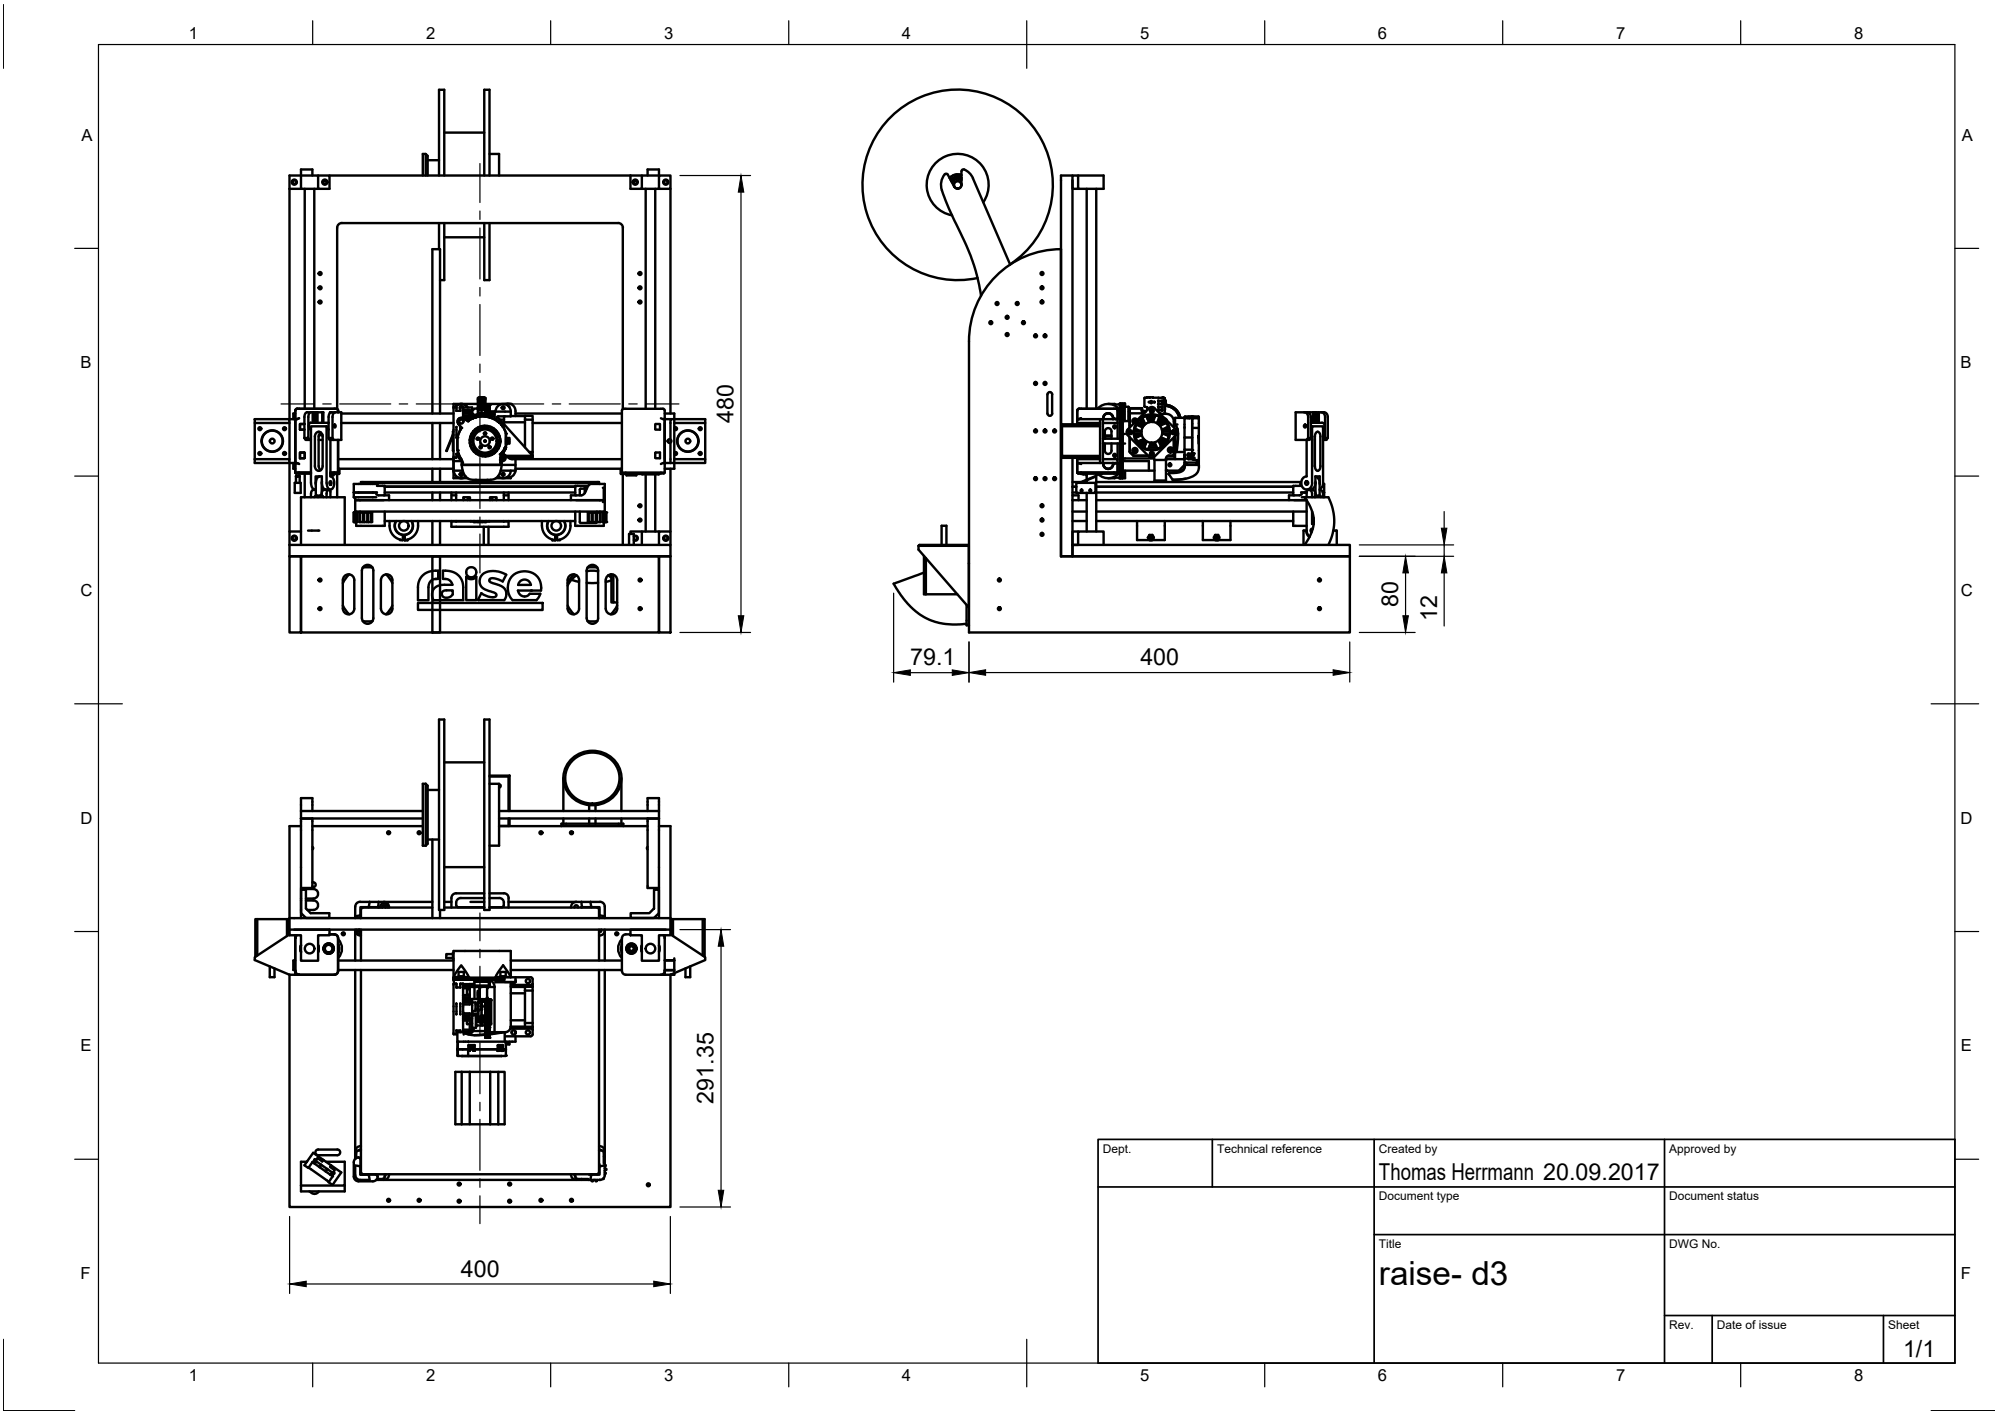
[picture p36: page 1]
Dept.; Technical reference; Created by; Approved by; Document type; Document status; Title; DWG No.; Rev.; Date of issue; Sheet; raise- d3; Thomas Herrmann 480

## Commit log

2017-09-28 Added "BOM"
2017-12-12 Nema 17 Holder, minor changes
    [#raiseuav komplett 2017_09_16.dxf, Bodenplatte.dxf, Cableduct_bed.stl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]
2017-12-18 Folder added
    [Aero_Frame.stl, Angle_Portal.stl, Axial_fan_shroud.stl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]
2018-01-02 Added BOM
2018-01-02 Bom updated
2018-01-09 Updated X-Carriage, X-Carraige_cable, Y Neam17 to latest
    [Nema17-Y-Stepper_Holder.stl, X-carriage.stl, X-carriage_cable.stl]
2018-01-09 Removed old Files
    [Axial_fan_shroud.stl, MK2B_Bett_small.stl, TuningKnob.stl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]
2018-01-09 deleted old files
    [Axial_fan_shroud.stl, TuningKnob.stl, Z-Adjust.stl]
2018-01-09 Updated and added parts to current
    [Aero_Frame.stl, Axialfan_Mount.stl, MK2B_Bett_small.stl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]
2018-02-07 Added new (Alternative) Belt Tensioning Parts for X and Y
    [Nema17-Y-Stepper_Holder_AdjustB.stl, X-Bearing_Holder_AdjustB(Alternat).stl, Y-608Adapter8-4.stl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]
